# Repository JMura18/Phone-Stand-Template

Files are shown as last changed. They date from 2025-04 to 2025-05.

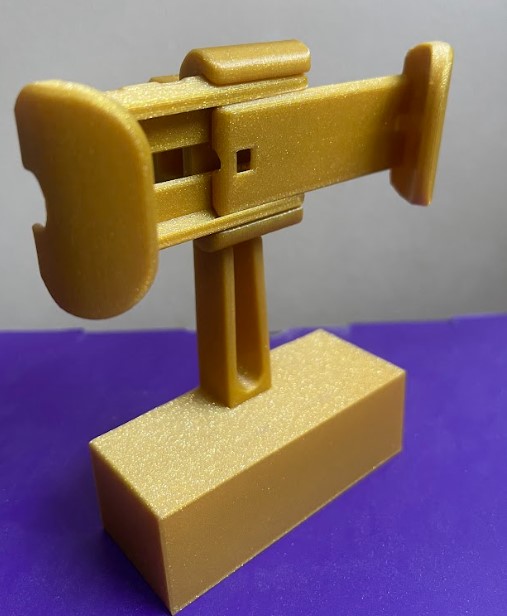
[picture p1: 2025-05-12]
Photos/Phone_Stand_Print.jpg

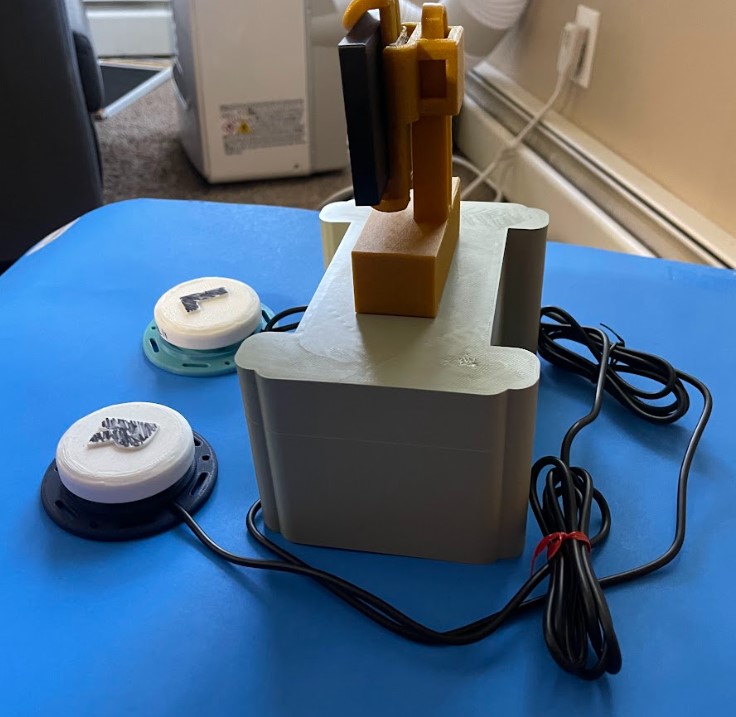
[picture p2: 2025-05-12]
Photos/Fully_assembled_topside.jpg

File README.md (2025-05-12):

<!--- TITLE --->
# Switch Operated Rotating Phone Stand 

## Overview
<!--- A brief summary of the project. What it does, who it is for, how much it costs. --->
In this project, we were able to create an automatic button-operated rotating camera stand. 

It makes it easier for photographers to make it easier for steady shots, either photo or video. 

The operating gear shifter is about $6.00. 



## Short Demo Video
https://github.com/user-attachments/assets/6819dd64-cb07-463f-bd0d-7a98d3ec8850

## How to Obtain the Device
### Do-it-Yourself (DIY) or Do-it-Together (DIT)

This is an open-source assistive technology, so anyone is free to build it. All of the files and instructions required to build the device are contained within this repository. Refer to the Build Instructions below.

## Build Instructions
<!--- Outline the major steps required to create a build --->

### 1. Order the Off-The-Shelf Components  
The [Servo_Phone_Stand_Bill_of_Materials.pdf](/Documentation/Servo_Phone_Stand_Bill_of_Materials.pdf) lists all of the parts and components required to build the device.

### 2. Print the 3D Printable Components  
All files are located in the [/Build_Files/3D_Printing_Files](/Build_Files/3D_Printing_Files/) folder.  
Use the [Servo_Phone_Mount_3D_Printing_Guide.pdf](/Documentation/Servo_Phone_Mount_3D_Printing_Guide.pdf) to guide your prints.

### 3. Assemble the Phone Stand  
Follow the [Rotating_Phone_Stand_Assembly_Guide.pdf](/Documentation/Rotating_Phone_Stand_Assembly_Guide.pdf) for step-by-step build instructions.

### 4. Read Through the User Guide  
The [Rotating_Phone_Stand_User_Guide.pdf](/Documentation/Rotating_Phone_Stand_User_Guide.pdf) contains detailed usage tips, safety information, and final setup/testing procedures to ensure the device functions as intended.

## How to Improve this Device
As open source assistive technology, you are welcomed and encouraged to improve upon the design. 

## Files
### Documentation
<!--- Update the name, link, and version for documentation --->

| Document | Version | Link |
|---|---|---|
| Design Rationale | 1.0 | [Rotating_Phone_Stand_Design_Rationale.pdf](/Documentation/Rotating_Phone_Stand_Design_Rationale.pdf) |
| 3D Printing Guide | 1.0 | [Servo_Phone_Mount_3D_Printing_Guide.pdf](/Documentation/Servo_Phone_Mount_3D_Printing_Guide.pdf) |
| Assembly Guide | 1.0 | [Rotating_Phone_Stand_Assembly_Guide.pdf](/Documentation/Rotating_Phone_Stand_Assembly_Guide.pdf) |
| Bill of Materials | 1.0 | [Servo_Phone_Stand_Bill_of_Materials.pdf](/Documentation/Servo_Phone_Stand_Bill_of_Materials.pdf) |
| User Guide | 1.0 | [Rotating_Phone_Stand_User_Guide.pdf](/Documentation/Rotating_Phone_Stand_User_Guide.pdf) |
| Maker Checklist | 1.0 | [Rotating_Phone_Stand_Maker_Checklist.pdf](/Documentation/Rotating_Phone_Stand_Maker_Checklist.pdf) |

### Design Files
<!--- Include a copy of the original design files to facilitate easy editing and customization. Consider also including a generic format (e.g., STEP) --->
- [Phone_Stand_Parts.obj](/Design_Files/Phone%20Stand%20Parts.obj)
- [Servo_Base.obj](/Design_Files/Servo_Base.obj)

### Build Files
<!--- Include a copy of the build files intended for manufacturing. This may include svg files for laser cutting, stl files for 3d printing, Gerber files for custom PCBs, and Arduino files for custom firmware. --->
- [Phone_Stand_Parts.stl](/Build_Files/3D_Printing_Files/Phone_Stand_Parts.stl)
- [Servo_Base.stl](/Build_Files/3D_Printing_Files/Servo_Base.stl)

## Attribution
<!--- Provide any necessary attribution for designs or components that are included in the device or as part of the project. --->
The device was designed by Jake Murakami, Noel Raehl, Ethan Caldecott, Devinn Chi. 

<!--- This is the attribution for the template. --->
The documentation was written by Jake Murakami, Noel Raehl, Ethan Caldecott, and Devinn Chi.

### Contributors
<!--- List the names of the people that contributed to the design. This could include the original source of the idea, designers, testers, documenters, etc. --->
Designers:
 - Devinn Chi 
 - Jake Murakami
 - Noel Raehl
 - Ethan Caldecott

Assisted with Soldering and Helping formulate Arduino code and related materials:
 - Dave Bailey

Outlined and Assisted with Overall Project:
 - Lauren Milne

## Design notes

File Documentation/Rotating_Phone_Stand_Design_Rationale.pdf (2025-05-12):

V 1.01 | May 2025

## Switch-Operated Rotating Phone Stand

## DESIGN RATIONALE

## Overview and Purpose of Our Project

The design problem we set out to solve was enabling photographers to capture steady images and videos without manually holding their phone. Many photographers struggle to hold their camera steady, particularly when taking panoramas or recording videos. Our solution was to create a fully functional rotation phone stand controllable with assistive switches and designed with accessibility, user convenience, and cost in mind. We followed a user-centered design process to ensure the final product would meet the real-world needs of photographers who would benefit from hands-free operation. In this document, we will reflect on each stage of the design process and how our decisions were grounded in design research, principles, and user feedback.

Throughout this project, we were intentional about rejecting outdated models of disability like charity and medical, which frame disabled users as passive recipients of aid or as problems to be fixed. We embraced it more from an inclusive framework, particularly looking at the social and identity models of disability. This model's main point is that disability arises from environmental mismatches and states that the environment is not well suited for the user, and this creates disability. We tried to create something like this that would expand the scope of the environment when it comes to photography, as we are not just making it easier to photograph; there is also a component of inclusivity that comes with an automatic phone stand that others don’t have.

Another aspect was Wobbrock’s ability-based design, Ladner’s emphasis on user empowerment, and Ko’s critique of design for the “average user.” We prioritized adaptability and personalization in our rationing phone stand. Rather than treat users as test subjects, we involved their input early, particularly during conversations with photographers like Jasper, who directly shared our design priorities for the phone, and when it comes to flexible sizing and mounting angles. We tried to make this a space of co-creation where we and the user worked together, giving the user visual and functional input into the device’s outcome. This was a big point we tried to incorporate throughout our testing.

## Design Process

Stage 1: Initial Design Exploration

Users will need access to a 3D printer to create this phone stand. The printers we used were the Prusa (https://www.prusa3d.com/?gad_source=1&gad_campaignid=805226342&gbraid=0AAAAADkiZoPqD3C0CF60OmRsSu5AudD7M) MK4 and the Prusa (https://www.prusa3d.com/?gad_source=1&gad_campaignid=805226342&gbraid=0AAAAADkiZoPqD3C0CF60OmRsSu5AudD7M) MK3S. The user will also need an Arduino board; we used the Sparkfun Redboard (https://www.sparkfun.com/sparkfun-redboard-programmed-with-arduino.html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) programmed with Arduino (https://www.arduino.cc/) because of its USB-C compatibility, which is almost universally compatible with any modern computer. You will need to download the Arduino IDE to program this board. You will also need 3.5mm jacks and copper wire for soldering. We designed this product to connect to 2 interactive switches (https://github.com/makersmakingchange/Interact-switch) from MakersMakingChange. The parts of this project that we designed or adapted are the Servo base

## DESIGN RATIONALE

and the Phone stand. We designed the Servo base – the component which holds the servo and hides the Arduino board + all of the wiring – using an online software called OnShape. (https://www.onshape.com/en/) This software allowed us to 3D model using exact measurements, which was how we held the Servo tightly. Here are images of the 3D model for the base:

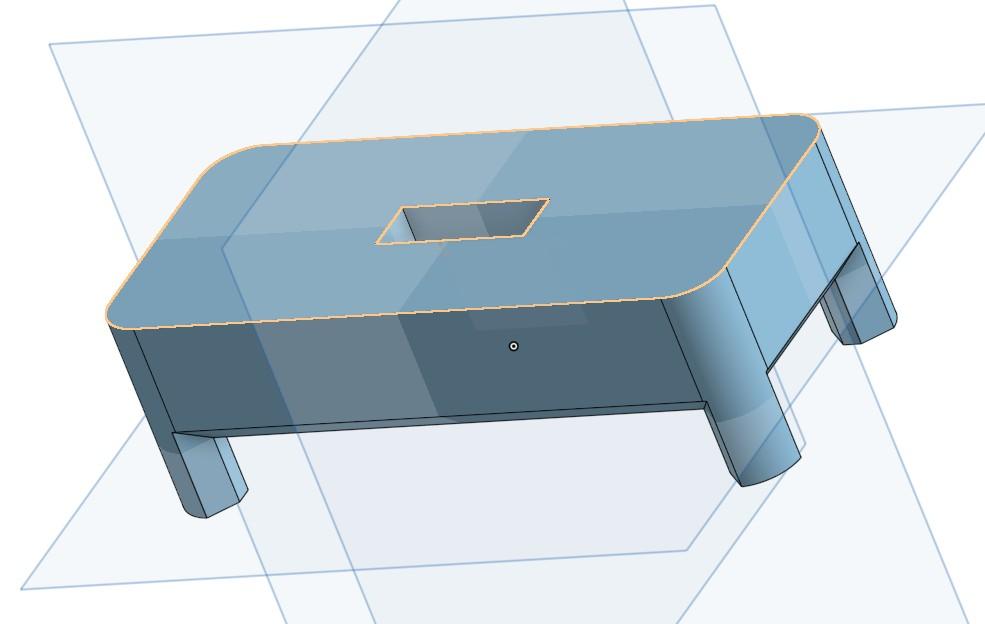
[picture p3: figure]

Next, we found an adjustable phone mounting system online on a website called Cults (link to design). (https://cults3d.com/en/3d-model/gadget/modular-mounting-system) We adapted parts of this model to create a phone stand that could securely attach to the head of our servo motor. The advantage of using this existing design was that it already supported adjustability for different phone sizes and angles. In construct, our original concept, a fixed cage-style holder sized for an iPhone 16 Pro Plus, lacked flexibility and failed to accommodate other devices, as shown here:

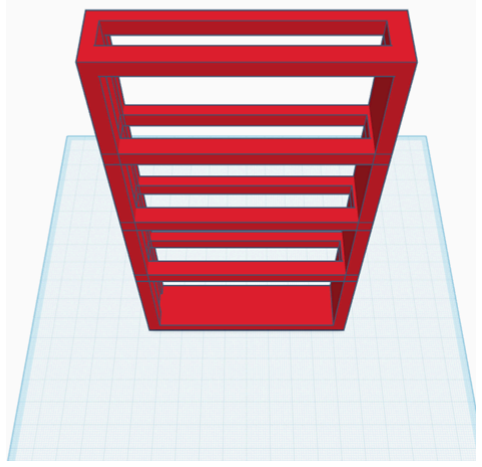
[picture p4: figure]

The inspiration came from a FaceTime call with a photographer named Jasper, who, when showing around, mentioned the lack of flexibility with phone sizing. Also, I want to show

## DESIGN RATIONALE

him the original concept and the ability to be vertical or horizontal. Here is what the new version, based on the Cult phone mounting system parts, looks like from a top and side view:

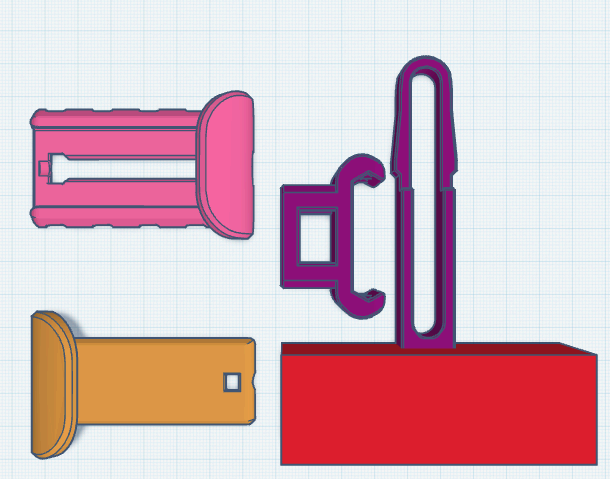
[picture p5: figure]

Stage 2: Assemble materials

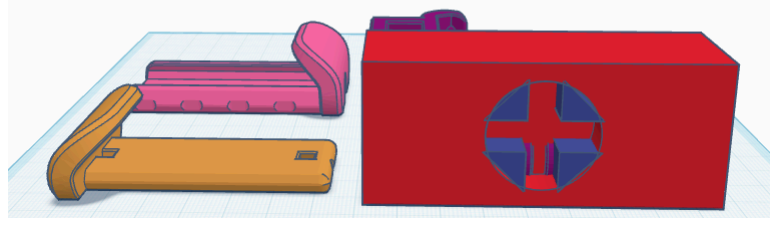
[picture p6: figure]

Once all parts of this phone stand have been gathered/printed (using our 3D print guide), the user needs to connect the two switches and the Servo motor to the Arduino board. The Servo’s ground should be connected to the Arduino, and the 5V power should be connected. Then, the user should use pin 9 to connect the Servo’s signal to the Arduino, allowing the Servo to receive inputs from our program. Once this is done, the user needs to connect the switches. To do this, the user will solder each switch to one end of a cable, the other ends will go into the same ground pin (not the same as the servo, but both 3.5mm connections should plug into the same ground as each other), and then each to its digital input pin. We used pins 11 and 12 for the switches, which you can see in our program. A link to the code we used to run this project is here. (https://github.com/JMura18/Phone-Stand-Template/blob/main/Code/Arduino_IDE_Code/Arduino_IDE_Code.ino) The code is quite simple; it takes input (HIGH or LOW) from the switches and then moves the Servo accordingly. Once the wiring is done, it should look something like this:

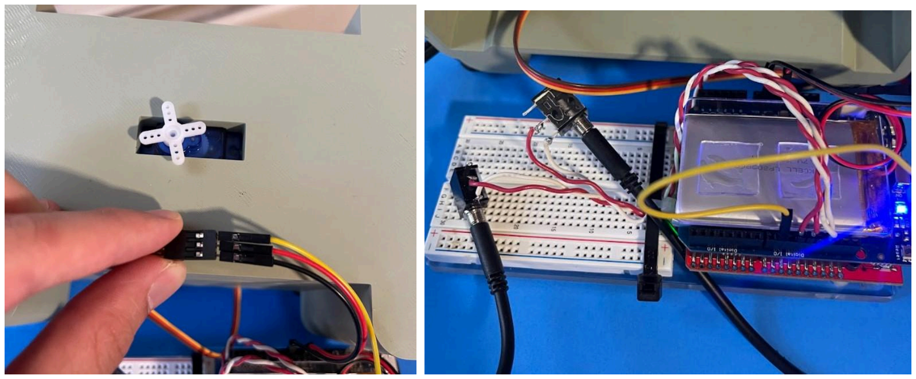
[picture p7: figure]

Stage 3: Iteration

Our group had to make changes based on our intuition because we could not complete our user testing before any iterations. One of our changes was to update the Servo base so that it

## DESIGN RATIONALE

was tall enough to cover the Arduino board completely and accommodate the wiring for the switches. This was done again using OnShape and by making some precise measurements. Here is what our final design looked like for the Servo base:

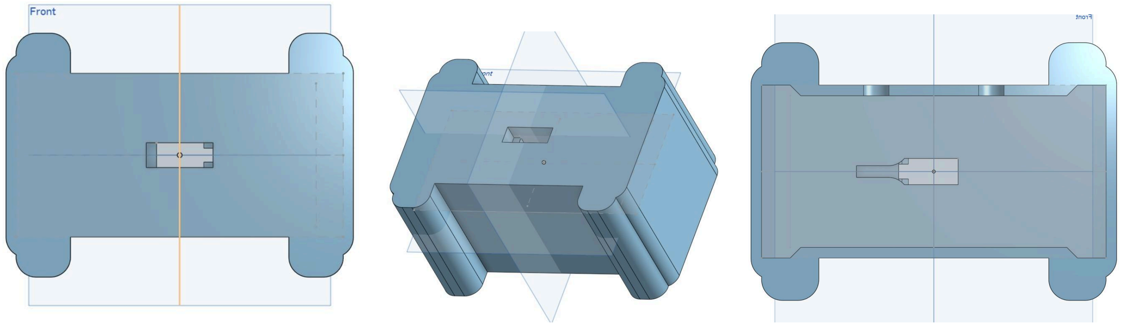
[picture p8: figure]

Our rationale behind this change was so that users can hide the messy wiring of the phone stand and protect the Arduino board from harm. Another adjustment we made was to the phone stand. This was previously mentioned, how we moved from a cage concept to a stand taht could adjust sizing and go horizontal and vertical. We had to make a minor tweak to the sizing of the servo, as the original attempt was too big and loose. Here is a photo of the adaptation we made so that the stand could fit on top of the Servo head:

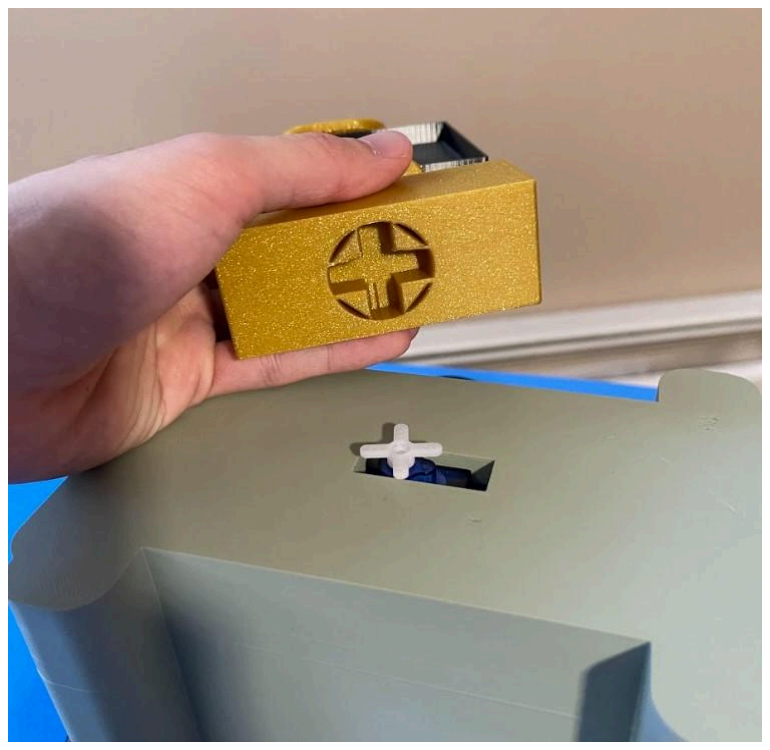
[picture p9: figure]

It is also important to note that our team had to modify our choice in Servo due to mechanical failure. Our initial Servo had 360-degree motion and was controlled using magnitude in a direction. This Servo broke for an unknown reason, so we had to purchase a different Servo with only 180 degrees of freedom, which used degrees as motion. While this is not technically an iteration, it is a design choice we had to make to have a functioning product by the end of our deadline.

## Conclusion and Future Improvements

Reflecting on our process, several key decisions stand out, like staying flexible, responding to and incorporating user feedback, and constantly adjusting our design choices. One surprise was the servo

## DESIGN RATIONALE

failure, which forced a last-minute change and highlighted the importance of designing for replacability because we designed for a generic servo shield, which allowed for easy replacement. While exploring various designs, we ultimately chose the options that best balance user comfort, affordability, and universal design. Our final prototype is a sprint in these categories and is easy to print and iterate upon.

We also tested the final product with a user named David, a photographer, who had never seen the device before. After trying it out, he said it was intuitive and worked as he thought it would. One future direction based on his feedback was to allow the user to go left or control the rotation speed of the servo. But overall, he was pleased with the button and the ability to turn your phone vertically or horizontally, which was intuitive and easy for him. Overall, the final user test validated that our phone stand was complete.

Even though the current version has limitations in terms of constant speed, this can be addressed in future iterations. We tried our best to build from an inclusive framework. That being said, one gap is in our process; we did not have access to users with physical disabilities. Thus, it is hard to know if we could truly accomplish the goal of an inclusive framework, outside of the fact that the user photograph we did say our design would work for someone with disability. If given more time, we would have tested on people with disabliy who are photographers as well and tried to design a speed toggle. Overall, this project we created made it easier for us to understand our user group and develop something that could be super practical for the average iPhone photographer.

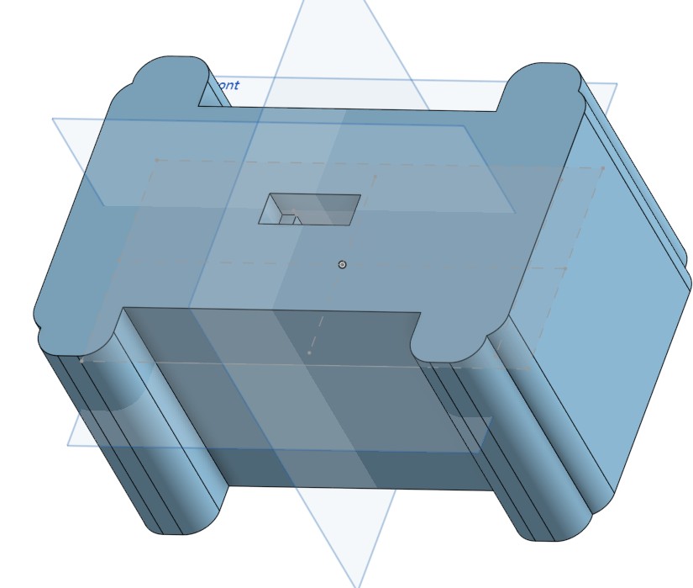
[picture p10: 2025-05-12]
Photos/3D model 2.jpg

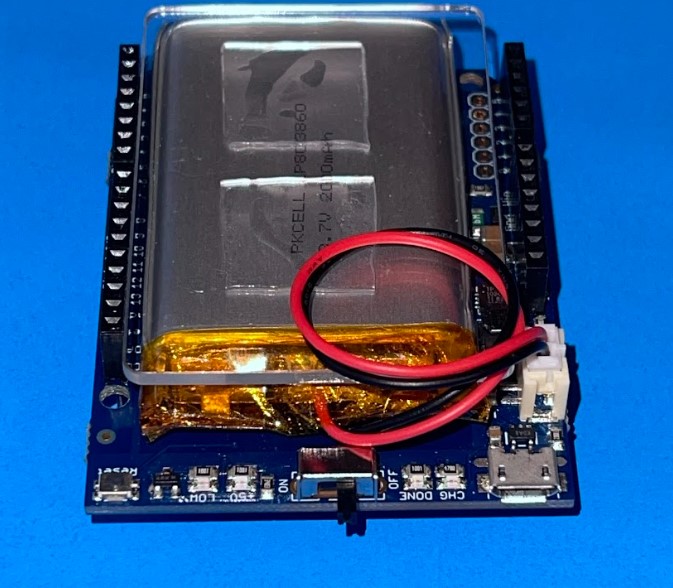
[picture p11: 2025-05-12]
Photos/Battery_Shield.jpg

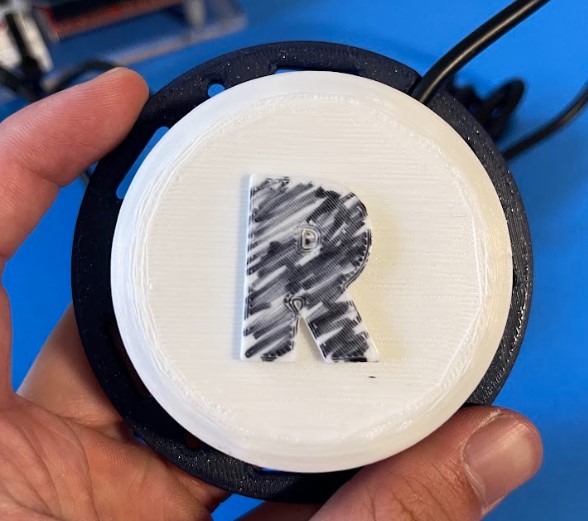
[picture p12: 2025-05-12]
Photos/Right_Button.jpg

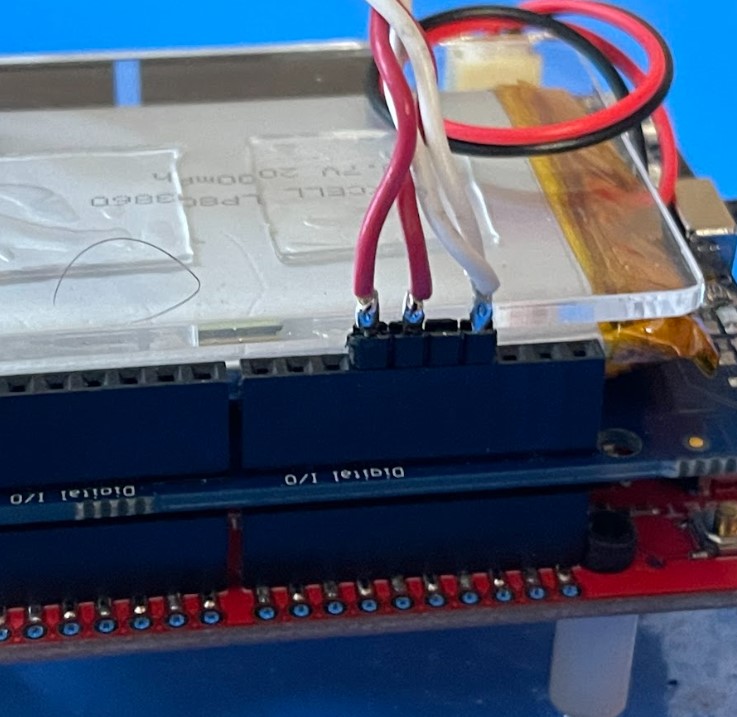
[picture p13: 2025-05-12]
Photos/Button_Connections.jpg

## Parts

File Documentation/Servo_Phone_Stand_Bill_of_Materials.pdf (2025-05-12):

Switch Adapted Servo Phone Stand | | Total Cost | | Total Print time (hr) | Total filament (g)
Version: V1.0.1 | Date Created: May 2025 | $ | 40.46 | 20.43 | 362.68
Part type (Electrical. Mechanical, Sanitization, ect) | | Quantity Needed | Pkg Quantity | Price per package | Price per Unit | Price for qty needed | Link
Inland KS0209 Blue 9g Servo Motor 1 1 $ 6.99 Arduino Uno (Sparkfun RedBoard) 1 1 $ 22.50 Copper Wire 1 100 $ 8.99 | | | | | $ 6.99 | $ 6.99 | Inland KS0209 Blue 9g Servo Motor (https://www.microcenter.com/product/613883/inland-ks0209-blue-9g-servo-motor) Arduino Uno (https://www.sparkfun.com/sparkfun-redboard-programmed-with-arduino.html) Copper Wire - Amazon (https://www.amazon.com/Copper-Gardening-Electroculture-Jewelry-Diameter/dp/B0C8SFPY7B)
| | | | | $ 22.50 | $ 22.50
| | | | | $ 0.09 | $ 0.09
3D Printed Parts ESTIMATED PRICING USING 1KG ROLL COST: | $ 30.00
Part | | Quantity Needed | TOTAL Mass (g) | Estimated Price | Print Time (Min)
Servo Base Mount | 1 | 261.84 | $ | 7.86 | 610
Adapted Phone Mount | 1 | 100.84 | $ | 3.03 | 616
| | Total Print Cost: | $ | 10.88
Alternatives
Part and description | Link
Servo Found on Amazon | Servo (https://www.amazon.com/WWZMDiB-SG90-Control-Servos-Arduino/dp/B0BKPL2Y21)

Commercial Parts:

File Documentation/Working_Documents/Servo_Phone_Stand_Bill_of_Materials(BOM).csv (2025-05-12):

Switch Adapted Servo Phone Stand |  | Total Cost | Total Print time (hr) | Total filament (g)
Version: V1.0.1 | Date Created: May 2025 | $40.46 | 20.43 | 362.68
Commercial Parts:
Part type (Electrical. Mechanical, Sanitization, ect) |  | Quantity Needed | Pkg Quantity | Price per package | Price per Unit | Price for qty needed | Link
Inland KS0209 Blue 9g Servo Motor |  | 1 | 1 | $6.99 | $6.99 | $6.99 | Inland KS0209 Blue 9g Servo Motor
Arduino Uno (Sparkfun RedBoard) |  | 1 | 1 | $22.50 | $22.50 | $22.50 | Arduino Uno
Copper Wire |  | 1 | 100 | $8.99 | $0.09 | $0.09 | Copper Wire - Amazon
3D Printed Parts ESTIMATED PRICING USING 1KG ROLL COST: | $30.00
Part |  | Quantity Needed | TOTAL Mass (g) | Estimated Price | Print Time (Min)
Servo Base Mount |  | 1 | 261.84 | $7.86 | 610
Adapted Phone Mount |  | 1 | 100.84 | $3.03 | 616
 |  |  | Total Print Cost: | $10.88
Alternatives
Part and description | Link
Servo Found on Amazon | Servo

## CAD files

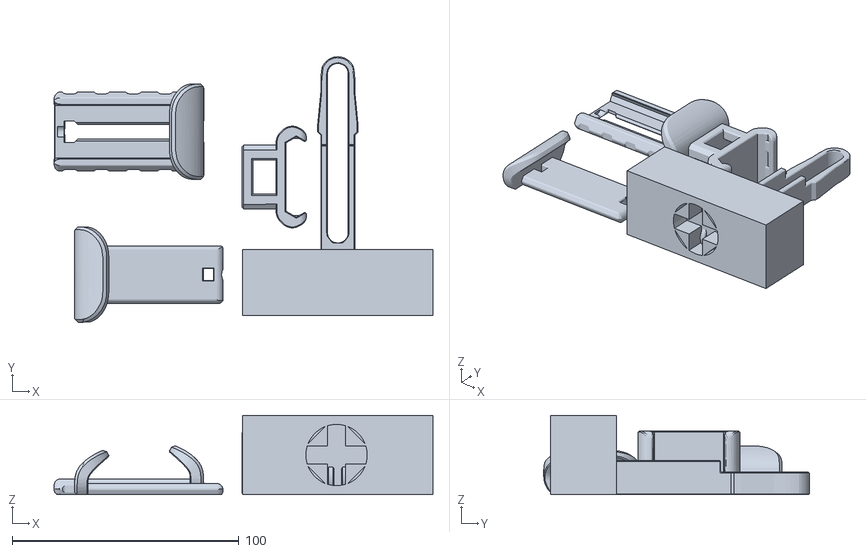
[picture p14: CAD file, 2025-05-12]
Build_Files/3D_Printing_Files/Phone_Stand_Parts.stl
167.0 x 117.0 x 35.0

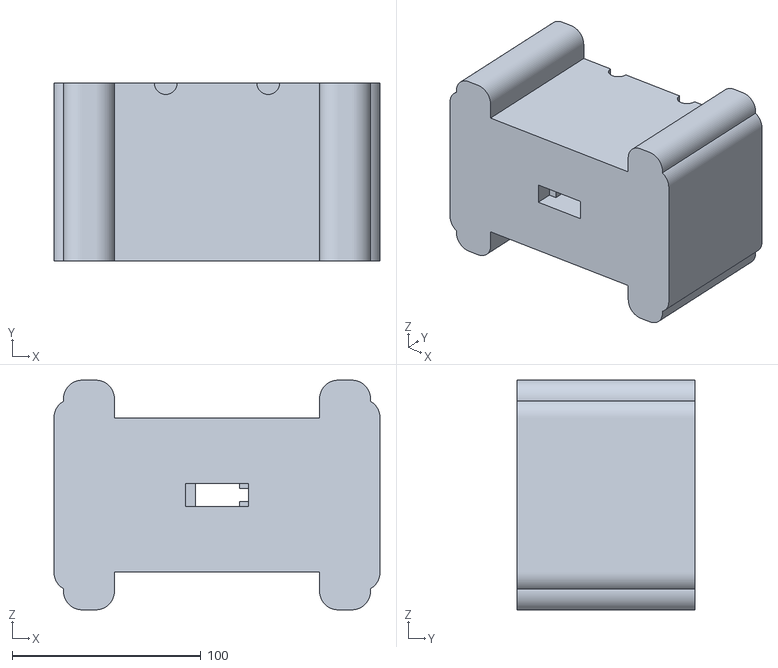
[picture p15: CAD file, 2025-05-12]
Build_Files/3D_Printing_Files/Servo_Base.stl
172.5 x 94.1 x 121.6

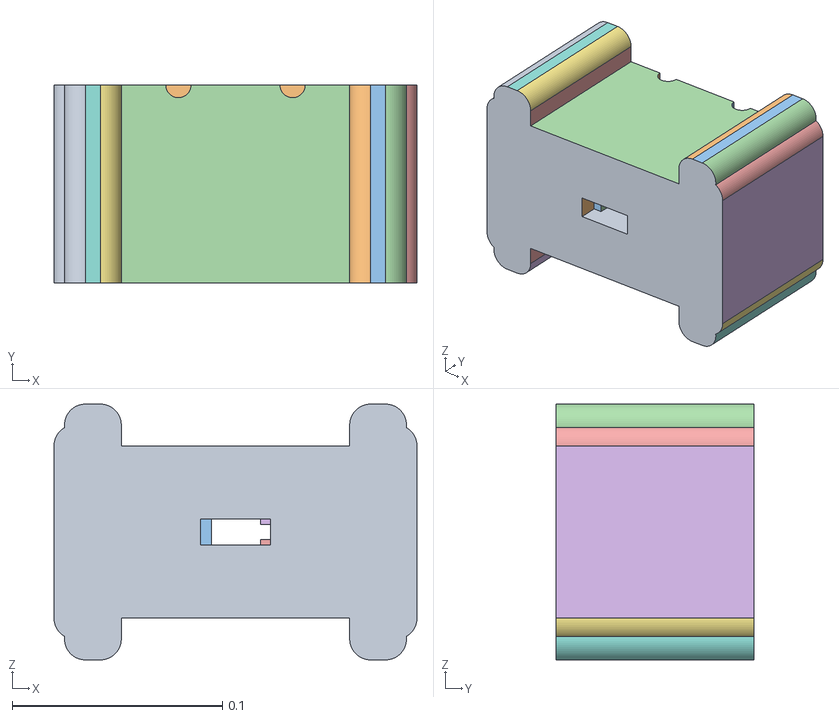
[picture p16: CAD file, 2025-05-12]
Design_Files/Servo_Base.obj
0.173 x 0.0941 x 0.122

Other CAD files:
Design_Files/Phone Stand Parts.obj

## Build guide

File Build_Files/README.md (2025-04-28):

<!--- Open Source Assistive Technology Template: GitHub Build_Files Readme Version 1.2 (2025-Feb-04)  --->
This folder contains the build file for the device, the .stl file for the base in the 3D_Printing_Files.

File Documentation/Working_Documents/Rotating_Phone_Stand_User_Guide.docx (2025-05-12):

# Overview

This document contains the necessary information to use the Switch-Operated Rotating Phone Stand, a rotating stand controlled by switches

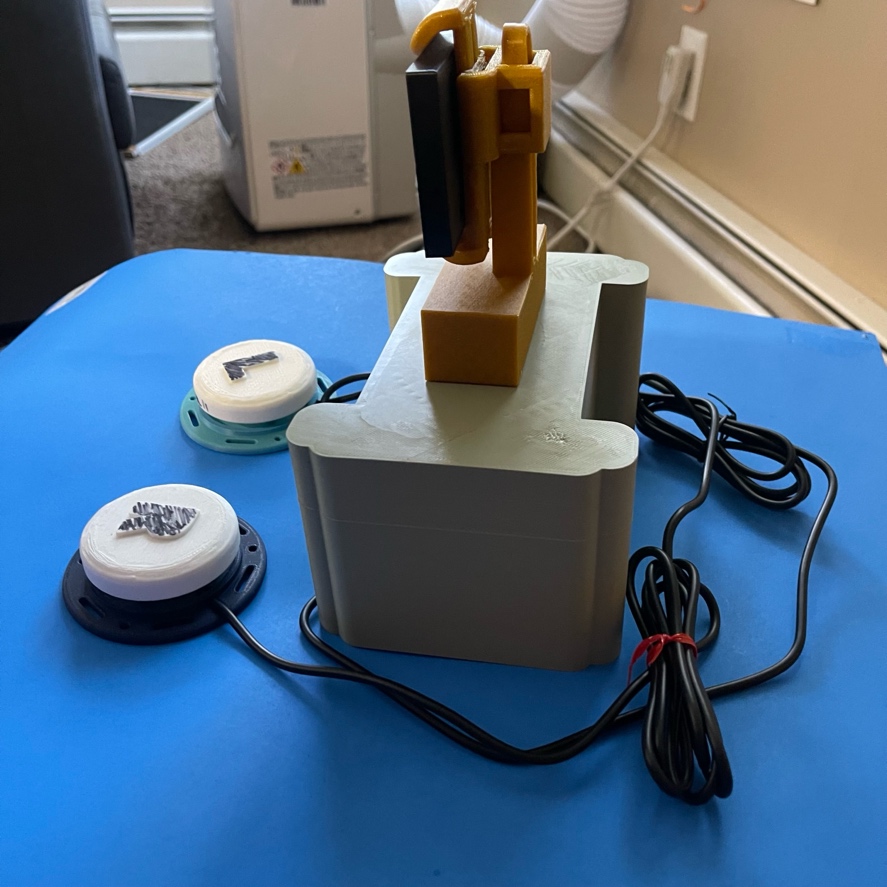
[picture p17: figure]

## Introduction

The Switch-Operated Rotating Phone Stand is a rotating phone stand controlled by two switches. It is designed to allow easy insertion, removal, and adjustment of the phone. This device is inspired by users on Makers Making Change and aims to assist individuals with limited mobility or one-handed use to easily use their phone.

### Features

The Switch-Operated Rotating Phone Stand has:

- A stable base: It stands firmly to hold the phone.
- An adjustable phone holder: It can hold phones of different sizes.
- Two switches for control: You use these to turn the phone.
- A raised phone position: It holds the phone up so you can see it better.

Item | Switch-Operated Rotating Phone Stand
Size (Length x Width x Height) [mm] | 183.975 x 178 x 68.602
Rotation Mechanism | Servo Motor
Control Method | Two Switches, Arduino Chip

### Compatibility

The Switch-Operated Rotating Phone Stand is designed for compatibility with various smartphones. Its adjustable phone holder accommodates different phone widths and heights. The device interacts with the user through two wired switches that control phone rotation, and the phone holder itself, which securely holds the phone.

### Usage

### Placing Your Phone: Gently widen the phone holder and place your phone inside. Make sure it's held securely.

- Use the two round switches to turn the phone. Press one switch to rotate it one way, and the other switch to rotate it the opposite way.
- Adjust the phone's position until you can see the screen comfortably.
- Carefully widen the holder and take your phone out.

Takedown:

- Remove the phone from the holder.
- Detach the rotating component from the base.

Storage & Care:

- Store the base, electrical components, and rotating component in a cool, dry place.
- Keep these parts in a location where they are protected from moisture.
- Store the components in a lower location or secure area to prevent them from falling and getting damaged.

The Rotating Phone Stand is made of 3D printed plastic. Exposure to high heat may cause warping and/or negatively affect function. Extended exposure to sunlight will also weaken the plastic on the device.

The Rotating Phone Stand contains electronics and is not waterproof. If the device becomes wet, make sure it is off and do not use it until it has completely dried. It may help to open any electronic enclosures to speed up drying and ensure it has completely dried.

Cleaning

The Rotating Phone Stand can be wiped with a damp cloth. The Rotating Phone Stand can also be cleaned by scrubbing with warm water and dish soap. Do not use hot water or clean in a dishwasher.

If using warm water and dishsoap, ensure any electronic components have been removed before washing.

### Disposal

PLA filament may be industrially compostable in your area. Check with your waste management company if PLA can be composted or must be thrown in the garbage.

Disassemble the Rotating Phone Stand and separate out the recyclable and compostable components, and those that must be thrown out. Electronics and batteries should be disposed of following your local waste management guidelines.

© <YEAR> by <AUTHOR> OR <Neil Squire>. This work is licensed under the CC BY SA 4.0 License: http://creativecommons.org/licenses/by-sa/4.0 Files available at <REPLACE WITH MMC GITHUB LINK> Page 1 of 5

© 2025 by Ethan Caldecott, Devinn Chi, Jacob Murakami, and Noel Raehl. This work is licensed under the CC BY SA 4.0 License: http://creativecommons.org/licenses/by-sa/4.0 Files available at <REPLACE WITH MMC GITHUB LINK> Page 1 of 5

V<X.Y.Z> | <MONTH> <YEAR> <PLACE LOGO HERE> <DEVICE NAME> USER GUIDE

V1.01 | May 2025 Switch-Operated Rotating Phone Stand USER GUIDE

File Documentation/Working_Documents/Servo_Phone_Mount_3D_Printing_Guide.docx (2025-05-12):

# 3D Printing Summary (Prusa MK4)

Metrics | Servo Base
Total Print Time (min) | 610min
Total Number of Components | 1
Typical Total Mass (g) | 261.84g
Typical Number of Print Setups | 1

# 3D Printing Summary (Prusa MK3S)

Metrics | Adapted Phone Mount
Total Print Time (min) | 616min
Total Number of Components | 1
Typical Total Mass (g) | 100.84 g
Typical Number of Print Setups | 1

# 3D Printing Settings (Prusa MK4)

Print File Name | Qty | Total Print Time (hr:min) | Mass (g) | Infill (%) | Support (Y/N) | Layer Height/ Nozzle Diameter (mm) | Notes (orientation, special settings, etc.)
Servo_Base.stl | 1 | 10:10 | 261.84g | 15 | Y (on build plate only) | 0.3/0.4 | Print in orientation given in STL Used 0.20mm STRUCTURAL rather than speed

# 3D Printing Settings (Prusa MK3S)

Print File Name | Qty | Total Print Time (hr:min) | Mass (g) | Infill (%) | Support (Y/N) | Layer Height/ Nozzle Diameter (mm) | Notes (orientation, special settings, etc.)
Phone Stand Parts.stl | 1 | 10:16 | 100.84g | 15 | Y (on build plate only) | 0.3/0.4 | Print in orientation given in STL Used 0.20mm QUALITY rather than speed

# Post-Processing

It is good to use supports for this device. I chose to let my slicer program, the Prusa slicer, automatically insert supports on the build plate only. I also chose to use 0.20mm structural/quality instead of speed, so that the build has a higher chance of being printed stably. I had access to two different printers, the MK4 and the MK3S, during this time. This is likely why the phone stand took so much longer, relatively, when comparing overall mass to the servo base. If printing using different printers, expect different speeds of printing.

# Customization Options

The user can request the color of the stand or any other custom markings they may want on the device.

# Examples of Quality Prints

Below are pictures of what the quality of the print is expected to look like:

Phone Stand:

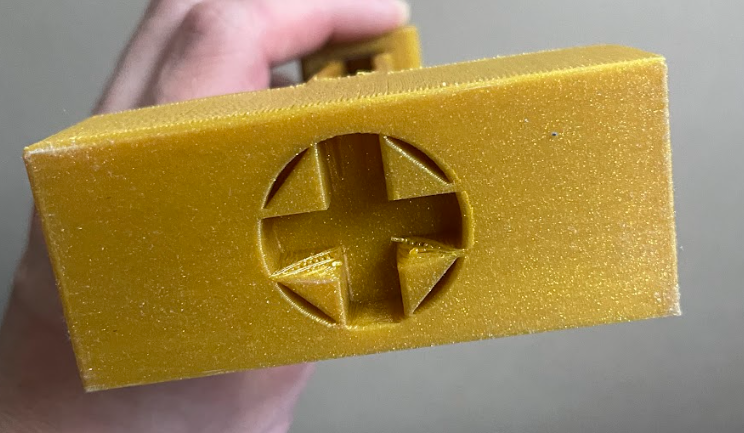
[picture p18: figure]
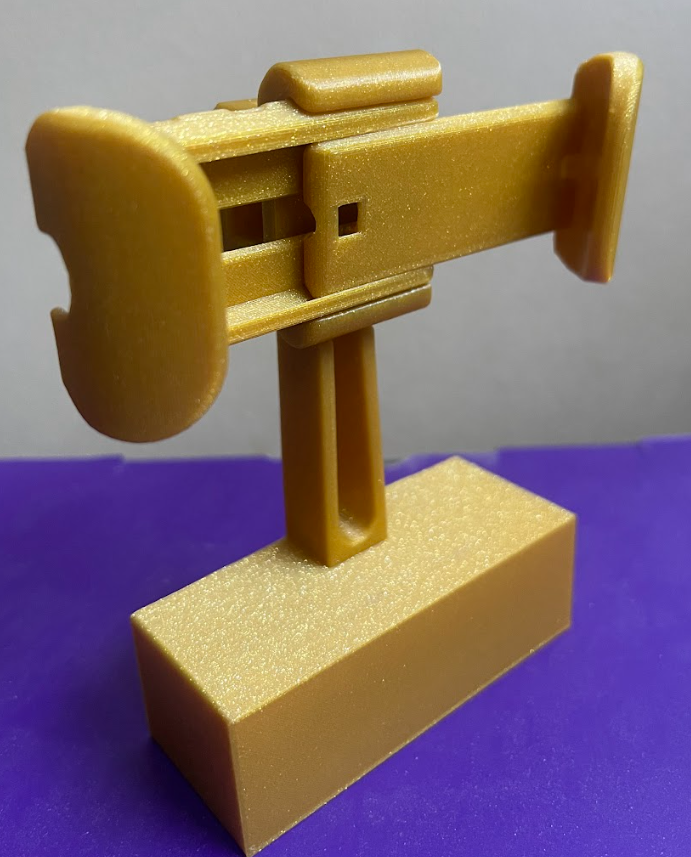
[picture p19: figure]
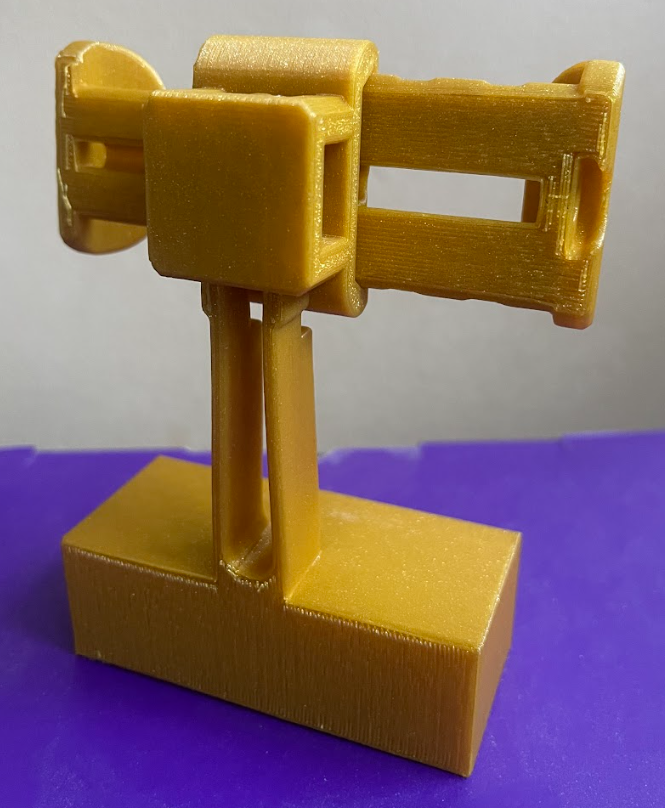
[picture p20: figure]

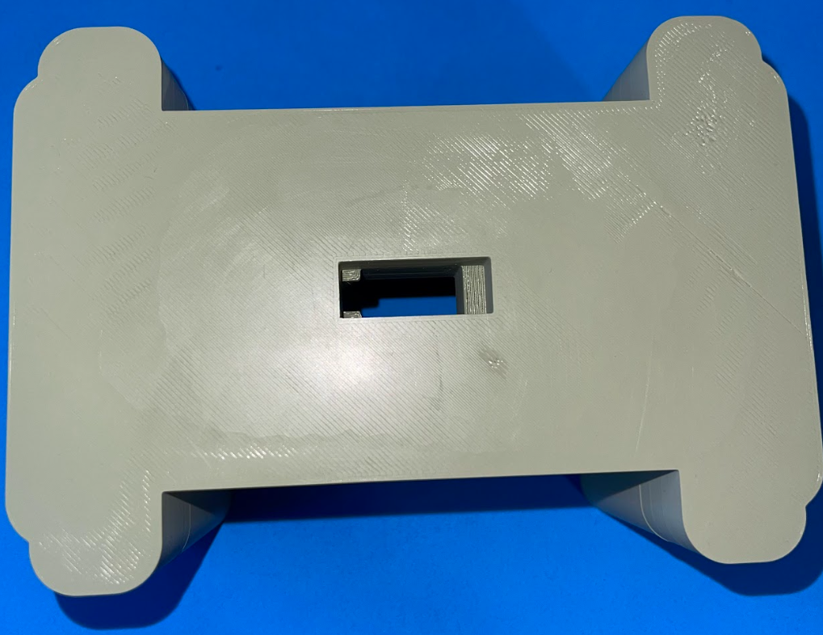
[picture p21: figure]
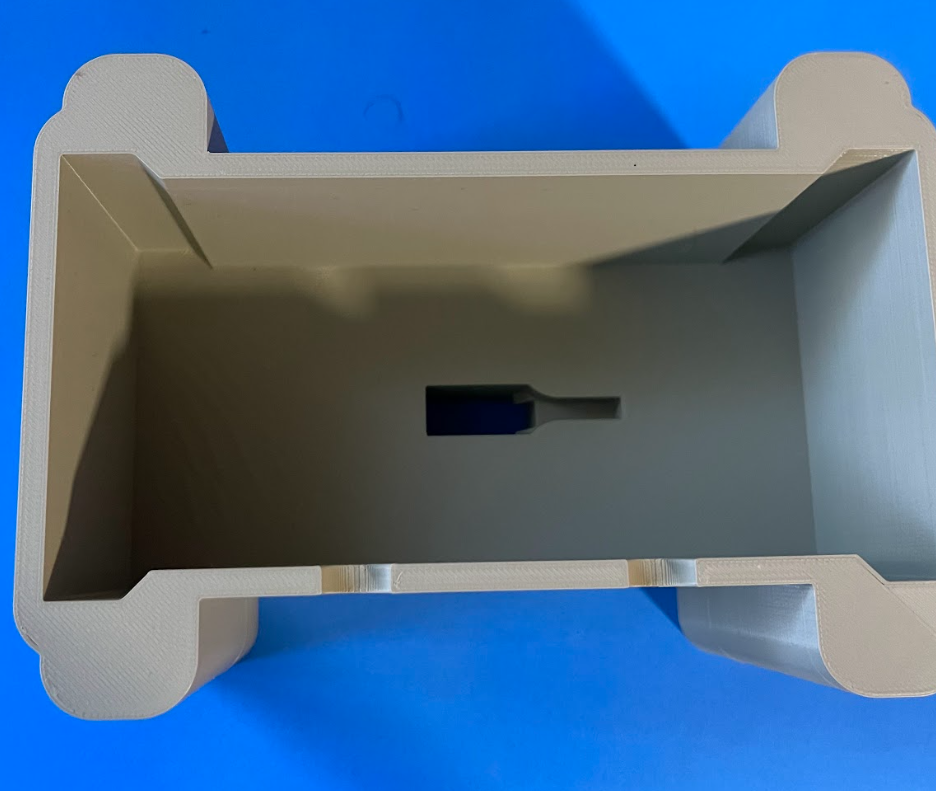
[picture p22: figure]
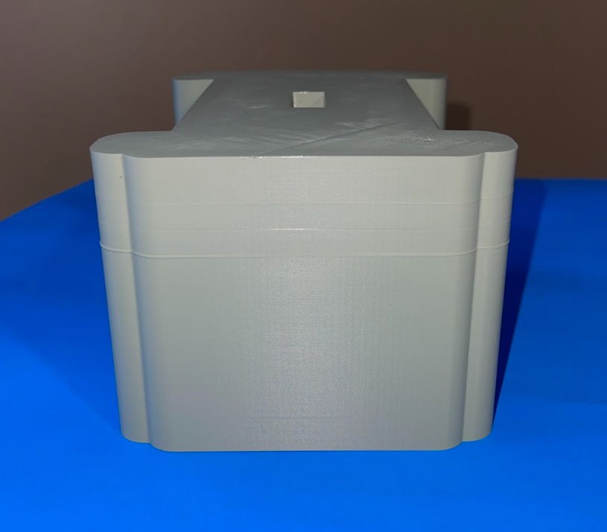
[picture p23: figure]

Servo Base:

© 2025 by Devinn Chi, Cat Martins, Noel Raehl – Macalester College This work is licensed under the CC BY SA 4.0 License: http://creativecommons.org/licenses/by-sa/4.0 Files available at https://github.com/davinchi73/Design_Sprint_3_Devinn-Cat-Noel Page 1 of 2

V1.0.1 | May 2025 Servo Phone Stand 3D Printing Guide

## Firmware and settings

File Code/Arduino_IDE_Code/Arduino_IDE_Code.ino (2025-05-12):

#include <Servo.h>

Servo myServo;

const int leftButtonPin = 11;
const int rightButtonPin = 12;
const int servoPin = 9;

int currentAngle = 90;      // Start at center
int targetAngle = 90;       // Desired angle

void setup() {
  pinMode(leftButtonPin, INPUT_PULLUP);
  pinMode(rightButtonPin, INPUT_PULLUP);
  myServo.attach(servoPin);
  myServo.write(currentAngle);
}

void loop() {
  bool leftPressed = digitalRead(leftButtonPin);
  bool rightPressed = digitalRead(rightButtonPin);

  if (leftPressed == LOW) {
    targetAngle = 0;  // move left
  } else if (rightPressed == LOW) {
    targetAngle = 180;  // move right
  } else {
    targetAngle = currentAngle;
  }

  // move left toward the target angle
  if (currentAngle < targetAngle) {
    currentAngle++;
    myServo.write(currentAngle);
    delay(10);  
  } else if (currentAngle > targetAngle) {
    currentAngle--;
    myServo.write(currentAngle);
    delay(10);
  }

  // If angles are equal, do nothing
}

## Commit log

2025-05-12 a bunch of file deletes and adds
    [Phone Stand Parts (1).stl, Servo_Base.obj, Servo_Base.stl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]
2025-05-12 file rename
    [Phone Stand Parts.stl]
2025-05-12 obj for phone stand parts
    [Phone Stand Parts.obj]
2025-05-12 Assembly + User Guide
2025-05-12 create arduino code
